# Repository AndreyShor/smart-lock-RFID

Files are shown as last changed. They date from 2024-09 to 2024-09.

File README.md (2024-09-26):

# RFID Lock System

## RFID Lock on ESP 8266 (Wemos D1 min)

Wifi version of the RFID system is working on Wemos D1 mini microcontroler.

Templates for 3D Printer is stored in "Case" foldier. This files can be used to 3d print case for the lock.

We was using Arduino framework in combination with C++ libraries to write code for microcontroller.

<strong>LED Commands: </strong>
<ul>  
 <li>1 long blink - door is open </li>
 <li>2 short blings - incorrect RFID card </li>
 <li>Lock is blinking non stop - lock is trying to connect to WIFI </li>
 <li>8 medium blinks and 2 short - lock is connected to Wifi bet can't access server </li>
</ul>

## Lock Side Code - C/C++ and Arduino

Microcontroller is used on lock side. Basic Function of microcontroller is to get UID of a user and send it to the server for validation and manipulate a relay of the lock.

<strong> Link to all libraries for Microcontroller: </strong>

    \\cseesrv04\tech\CSEEprojects\RFID Lock Library

<ol>

<li> <strong> RFID_TAG_UID_PRINT.ino </strong>- contains code to display UID of the tag. </li> 

<li> <strong>DB</strong> - contains files of DB design </li> 

<li> <strong>Authentication_system.ino</strong> - contains authentication systemm for ESP8266, it is validate user by UID stored in in MySQL datbase and opening door for 5 seconds. Data encrypted done by using AES-128 algorithm </li> 

<li> <strong>ESPwifi_http_connection.ino</strong> - contains code to send request to connect to Wi-Fi, send request to backend server, store data in local memory 
<ol> You must specify
<li><strong>ssid</strong> of Wi-fi </li>
<li><strong>password</strong> of Wi-fi </li>
<li><strong>server IP</strong> and path to send request</li>

 </ol>

</li> 

</ol>

## Backend - Server Side,JavaScript Node.js, Express, MySQL 

Backend is written on Node.js + Express framework. MySQl is used as a Databse. Server is written on REST architecture.

Server is proccesing all request from the lock and grant access to space. 

Versions:
<ol>
<li>Node.js - 19.6.1</li>
<li>Npm - 9.5.0</li>
<li>Express - 4.18.2</li>
<li>mysql2 -3.2.0 </li>
 </ol>

All code you can find in a foldier "Server-Backend"

<strong>Environment and package varibles</strong> is specified in <strong>package.json</strong> file

<strong>Connection to MySQL <strong/> is specified in "DB/connect_db.js"

<strong>Authentication keys for AES is specified in "controller/cryptography.js"

You can <strong>create database and table </strong>by running create_db.sql

All <strong>server routes </strong> is specified in routes.js

You can start server by typing "npm start" or "node server.js"

### How to install node.js and npm

#### Short Way

<p>You should be able to install all libraries by copying project from /Server-Backend
Use this 2 commands to install everething, Node and NPM should be installed for this method </p>

    1. npm init
    2. npm install or npm i 

#### Long Way

<ol>
<li> Node.js and NPM - follow this link and install LTS version of node.js </li>
    https://nodejs.org/en/download

<li>NVM (Node Version Manager ) - install NVM to change version of Node.js to 19.6.1 or any others. Code should work on any versions of Node </li>

    https://github.com/nvm-sh/nvm

    Command to install nvm:
    npm i -g nvm

<li>Express - install express, this framework simplify routing on Node.js </li>
    https://expressjs.com/
    npm i -g express

<li>MySQL library</li>
    npm i mysql2
    https://www.npmjs.com/package/mysql2
 </ol>

## Electrical part of RFID lock 

Box, lead and frame was design for this project. Tou can find .stl and .gz files in <strong> Case foldier </strong>

Schematic of circuit:

Diagram

### Parts
<ol>
<li><strong> RELAY</strong> - KY-019 5V 1-Channel Relay Board Module for Arduino IOT, cost about 2 pounds </li>
<li><strong> Microcontroller</strong> - ESP8266, cost about 8 pounds </li>
<li><strong> RFID Reader</strong> - AZDelivery RFID Kit - MFRC522, about 4.5 pounds  </li>
<li><strong> DC-DC converter</strong> - 20W Adjustable DC-DC Buck Converter with Digital Display about 4.5 pounds </li>
<li><strong> Fuse</strong> </li>
<li><strong> Wifi Box</strong> - 3D printed </li>
<li><strong> Wifi Box Lead</strong> - 3D printed </li>
<li><strong> Wifi Box Frame</strong> - 3D printed </li>
<li><strong> Diode for lock</strong> - 0.2 pound </li>
<li><strong> Total Cost of RFID soluion:</strong> +- 20 pounds </li>

<li><strong>Lock</strong> - GEM GK310LS 12 VDC Electric Release, aboyt 50-60 pounds </li>
<li><strong>Total Cost of RFID soluion + Lock for 1 door:</strong> +- 70 - 80 pounds </li>
</ol>

### Pins

<p>You can find pins connection for ESP8266 and RFID Reader in ESP8266 Pins.docx</p>

# Encryption - C Language

## Encryption is build by using BearSSL framework written on C
<p>Link: </p>
<p>https://bearssl.org/ </p>

<p>I was using AES-128-CBC method of encryption.</p>

<p>Youd should make some minor changes to run code with ESP8266 </p>
<ul>

<li>0. Install MFRC522 for scanner </li>

<li>1. Add Base64A.h and Base64A.cpp files to C:\Users\%UserName%\AppData\Local\Arduino15\packages\esp8266\hardware\esp8266\3.1.2\cores\esp8266</li>
<li>2. Change Secret Key and IV Vector in Authentication_system.ino</li>

    uint8_t cipher_key[16] = {0, 2, 4, 3, 4, 5, 6, 7, 8, 9, 10, 11, 12, 13, 14, 15};
    uint8_t cipher_iv[16] = {0, 6, 6, 3, 4, 5, 6, 7, 8, 9, 10, 11, 12, 13, 14, 15};

<li>3. Change Secret Key and IV Vector cryptography.js</li>

    var cipher_key = Buffer.from([0, 2, 4, 3, 4, 5, 6, 7, 8, 9, 10, 11, 12, 13, 14, 15]);
    var cipher_iv = Buffer.from([0, 6, 6, 3, 4, 5, 6, 7, 8, 9, 10, 11, 12, 13, 14, 15]);

<li>3. Change IP Adress and port of server in Authentication_system.ino</li>

    String serverName = "http://192.168.0.102:8080/validateAccess";

<li>4. Change Wifi SSID and PASS in Authentication_system.ino</li>

    char* ssid = "TP-LINK_6926";
    char* password = "29328123";

</ul>

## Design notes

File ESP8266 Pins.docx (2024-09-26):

# RC522 Pins

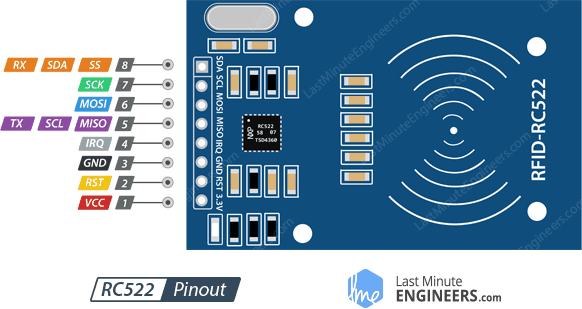
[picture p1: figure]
RC522 RFID Reader Writer Module Pinout

SS / SDA / Rx pin acts as a signal input when the SPI interface is enabled, as serial data when the I2C interface is enabled and as a serial data input when the UART interface is enabled. This pin is usually marked by encasing the pin in a square so that it can be used as a reference to identify other pins.

(IN) D2

SCK (Serial Clock) accepts the clock pulses provided by the SPI bus master i.e. Arduino. (Synchronization between controller and Arduino) D5

MISO / SCL / Tx pin acts as master-in-slave-out when SPI interface is enabled, as serial clock when I2C interface is enabled and as serial data output when the UART interface is enabled. (OUT) D6

IRQ is an interrupt pin that alerts the microcontroller when an RFID tag is in the vicinity. (Interrupt) NONE

GND is the ground pin and needs to be connected to the GND pin on the Arduino. (ground) GND

RST is an input for reset and power-down. When this pin goes low the module enters power-down mode. In which the oscillator is turned off and the input pins are disconnected from the outside world. Whereas the module is reset on the rising edge of the signal. (Shut down, reset) RST D1

VCC supplies power to the module. This can be anywhere from 2.5 to 3.3 volts. You can connect it to the 3.3V output from your Arduino. But remember that connecting it to the 5V pin will probably destroy your module! (power) 3.3V

ESP8266 Pin reference

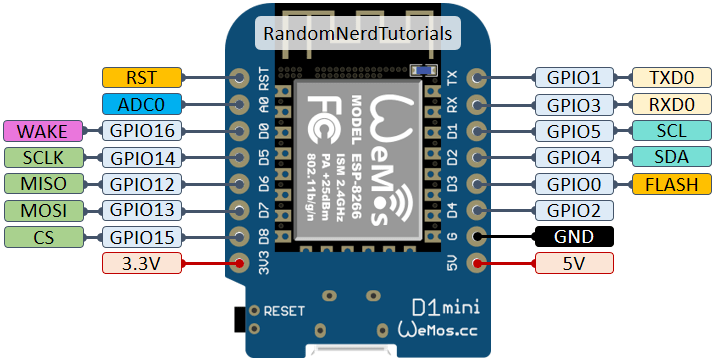
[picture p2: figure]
ESP8266 Pinout Reference: Which GPIO pins should you use? | Random Nerd Tutorials

Pin | Function | ESP-8266 Pin
TX | TXD | TXD
RX | RXD | RXD
A0 | Analog input, max 3.3V input | A0
D0 | IO | GPIO16
D1 | IO, SCL | GPIO5
D2 | IO, SDA | GPIO4
D3 | IO, 10k Pull-up | GPIO0
D4 | IO, 10k Pull-up, BUILTIN_LED | GPIO2
D5 | IO, SCK | GPIO14
D6 | IO, MISO | GPIO12
D7 | IO, MOSI | GPIO13
D8 | IO, 10k Pull-down, SS | GPIO15
G | Ground | GND
5V | 5V | -
3V3 | 3.3V | 3.3V
RST | Reset | RST

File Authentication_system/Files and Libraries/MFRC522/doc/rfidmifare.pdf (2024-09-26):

## Using a MFRC522 reader to read and write MIFARE RFID cards

on ARDUINO through the MFRC522 library BY COOQROBOT.
Mario Capurso (m.capurso@libero.it)

MIFARE is the NXP Semiconductors-owned trademark of a series of chips widely
used in contactless smart cards and proximity cards. According to the producers, billions of smart card chips and many millions of reader modules have been sold. [1]

The technology is owned by NXP Semiconductors (spin off from Philips Electronics in 2006) with headquarters in Eindhoven, Netherlands, and main business sites in Nijmegen, Netherlands, and Hamburg, Germany.

The MIFARE name covers proprietary technologies based upon various levels of the ISO/IEC 14443 Type A 13.56 MHz contactless smart card standard.
The MIFARE name (derived from the term MIkron FARE Collection System) covers
seven different kinds of contactless cards.

MIFARE Classic employs a proprietary protocol compliant to parts (but not all) of ISO/IEC 14443-3 Type A, with an NXP proprietary security protocol for authentication and ciphering.

The MIFARE Classic card is fundamentally just a memory storage device, where the memory is divided into segments and blocks with simple security mechanisms for access control. They are ASIC-based and have limited computational power. Thanks
to their reliability and low cost, those cards are widely used for electronic wallet, access control, corporate ID cards, transportation or stadium ticketing.

The MIFARE Classic 1K offers 1024 bytes of data storage, split into 16 sectors; each sector is protected by two different keys, called A and B. Each key can be programmed to allow operations such as reading, writing, increasing valueblocks, etc. MIFARE Classic 4K offers 4096 bytes split into forty sectors, of which 32 are same size as in the 1K with eight more that are quadruple size sectors. MIFARE Classic mini offers 320 bytes split into five sectors.

For each of these card types, 16 bytes per sector are reserved for the keys and access conditions and can not normally be used for user data. Also, the very first 16 bytes contain the serial number of the card and certain other manufacturer data and are read only. That brings the net storage capacity of these cards down to 752 bytes for MIFARE Classic 1k, 3440 bytes for MIFARE Classic 4k, and 224 bytes for Mini. It uses an NXP proprietary security protocol (Crypto-1) for authentication and ciphering.

The encryption used by the MIFARE Classic card uses a 48 bit key. [18]
A presentation by Henryk Plötz and Karsten Nohl[19] at the Chaos Communication Congress in December 2007 described a partial reverse-engineering of the algorithm used in the MIFARE Classic chip. Abstract and slides[20] are available online. A paper that describes the process of reverse engineering this chip was published at the August 2008 USENIX security conference.[21] (https://www.usenix.org/legacy/events/sec08/tech/full_papers/nohl/nohl.pdf)

In March 2008 the Digital Security[22] research group of the Radboud University Nijmegen made public that they performed a complete reverse-engineering and
were able to clone and manipulate the contents of an OV-Chipkaart which is a MIFARE Classic card.[23] (http://www.cs.ru.nl/~flaviog/publications/Talk.Mifare.pdf) For demonstration they used the Proxmark device, a 125 kHz / 13.56 MHz research instrument.[24] The schematics and software are released under the free GNU General Public License by Jonathan Westhues in 2007. They demonstrate it is even possible to perform card-only attacks using just an ordinary stock-commercial NFC reader in combination with the libnfc library.

In April 2009 new and better card-only attack on MIFARE Classic has been
found. It was first announced at the Rump session of Eurocrypt 2009.[35] This attack was presented at SECRYPT 2009.[36] The full description of this latest and fastest attack to date can also be found in the IACR preprint archive.[37] The new attack improves by a factor of more than 10 all previous card-only attacks on MIFARE Classic, has instant running time, and it does not require a costly precomputation.

The new attack allows to recover the secret key of any sector of MIFARE Classic card via wireless interaction, within about 300 queries to the card. It can then be combined with the nested authentication attack in the Nijmegen Oakland paper to recover subsequent keys almost instantly. Both attacks combined and with the right hardware equipment such as Proxmark3, one should be able to clone any MIFARE Classic card in not more than 10 seconds. This is much faster than previously thought.

The MFRC522 is a highly integrated reader/writer IC for contactless communication at 13.56 MHz. The MFRC522 reader supports ISO/IEC 14443 A/MIFARE mode.
The MFRC522’s internal transmitter is able to drive a reader/writer antenna designed to communicate with ISO/IEC 14443 A/MIFARE cards and transponders without additional active circuitry. The receiver module provides a robust and efficient implementation for demodulating and decoding signals from ISO/IEC 14443 A/MIFARE compatible cards and transponders. The digital module manages the complete ISO/IEC 14443 A framing and error detection (parity and CRC) functionality.

The MFRC522 supports all variants of the MIFARE Mini, MIFARE 1K, MIFARE 4K, MIFARE Ultralight, MIFARE DESFire EV1 and MIFARE Plus RF identification protocols. To aid readability throughout this data sheet, the MIFARE Mini,

MIFARE 1K, MIFARE 4K, MIFARE Ultralight, MIFARE DESFire EV1 and MIFARE Plus products and protocols have the generic name MIFARE.

The following host interfaces are provided:

- Serial Peripheral Interface (SPI)
- Serial UART (similar to RS232 with voltage levels dependant on pin voltage supply)
- I2C-bus interface

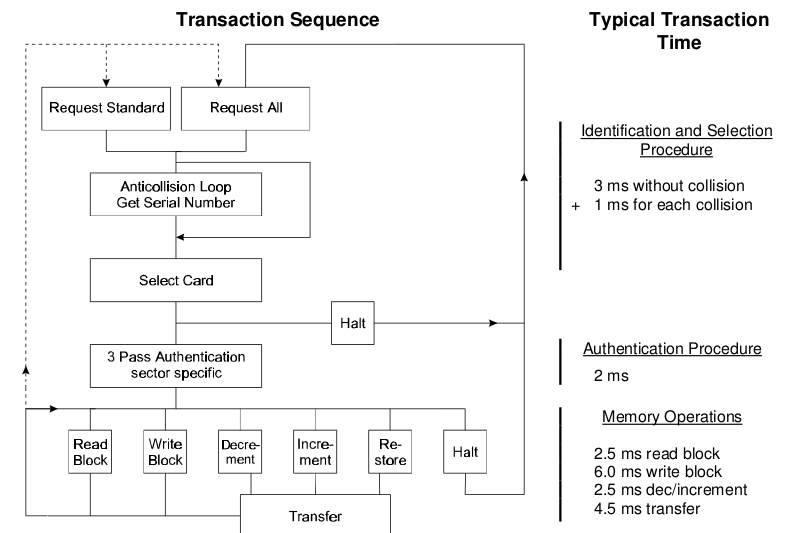
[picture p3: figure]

Answer to Request :

With the Answer to Request sequence the MIFARE® RWD (Read Write Device) requests all MIFARE® cards in the antenna field. When a card is in the operating range of a RWD, the RWD continues communication with the appropriate protocol.

Anticollision loop
In the Anticollision loop the serial number of the card is read. If there are several cards in the operating range of a RWD they can be distinguished by their different serial numbers and one can be selected (Select card) for further transactions. The unselected cards return to the standby mode and wait for a new Answer to Request and Anticollision loop.

Select Card
With the Select Card command the RWD selects one individual card for further authentication and memory related operations. The card returns the Answer to Select (ATS) code, which determines the individual type of the selected card.

Access Specification
After identification and selection of one card the RWD specifies the memory location of the following access.

Three Pass Authentication
The appropriate access key for the previously specified access is used for 3 Pass Authentication. Any communication after authentication is automatically encrypted at the sender and decrypted by the receiver.

Read/Write

After authentication any of the following operations may be performed:

READ | reads one block
WRITE | writes one block
DECREMENT | decrements the contents of one block and stores the result
| in the data-register
INCREMENT | increments the contents of one block and stores the result
| in the data-register
TRANSFER | writes the contents of the data-register to one block
RESTORE | stores the contents of one block in the data-register

The MF1ICS50 IC of a Mifare Classic has integrated a 8192 Bit EEPROM which is split into 16 sectors with 4 blocks. One block consists of 16 bytes (1 Byte = 8 Bit).

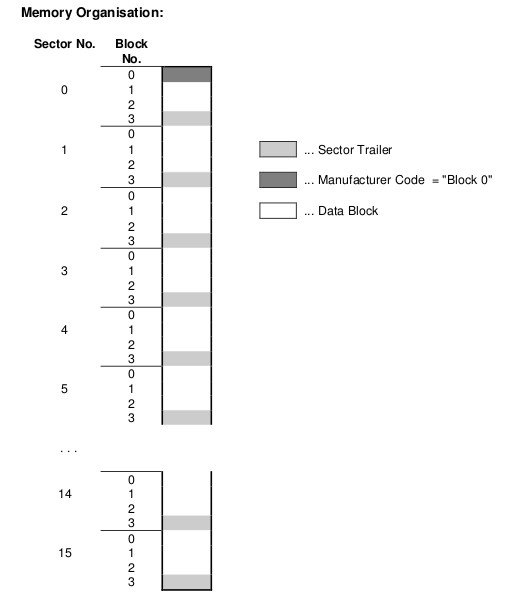
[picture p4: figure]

Manufacturer Code (Block 0 of Sector 0)

The first block of the memory is reserved for manufacturer data like 32 bit serial number. This is a read only block. In many documents it is named "Block 0".

Data Block (Block 0 to 3 except "Block 0")

Access conditions for the Data Blocks are defined in the Sector Trailers. According to these conditions data can be read, written, incremented, decremented, transferred or restored either with Key A, Key B or never.

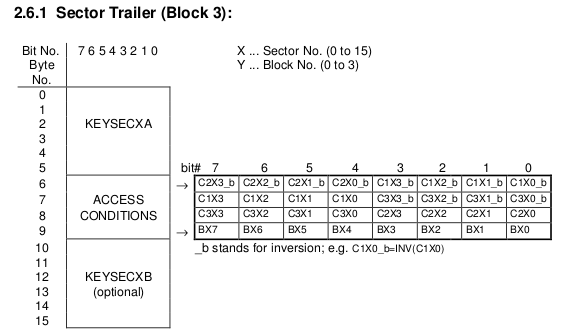
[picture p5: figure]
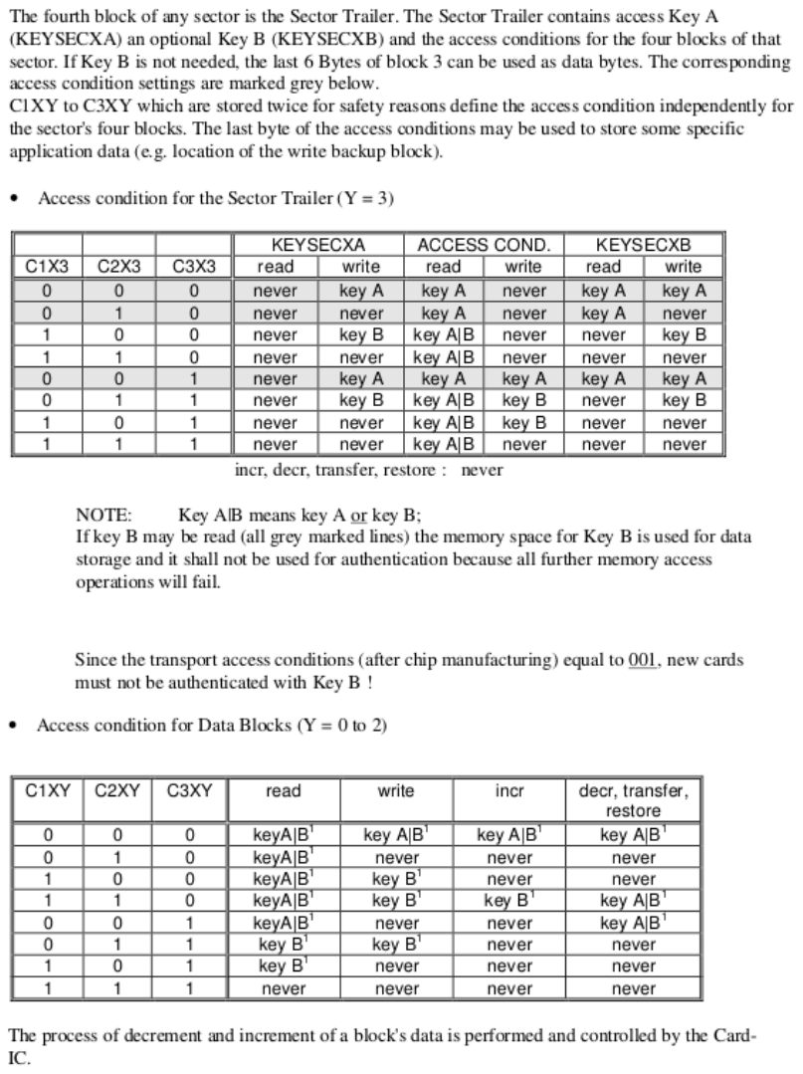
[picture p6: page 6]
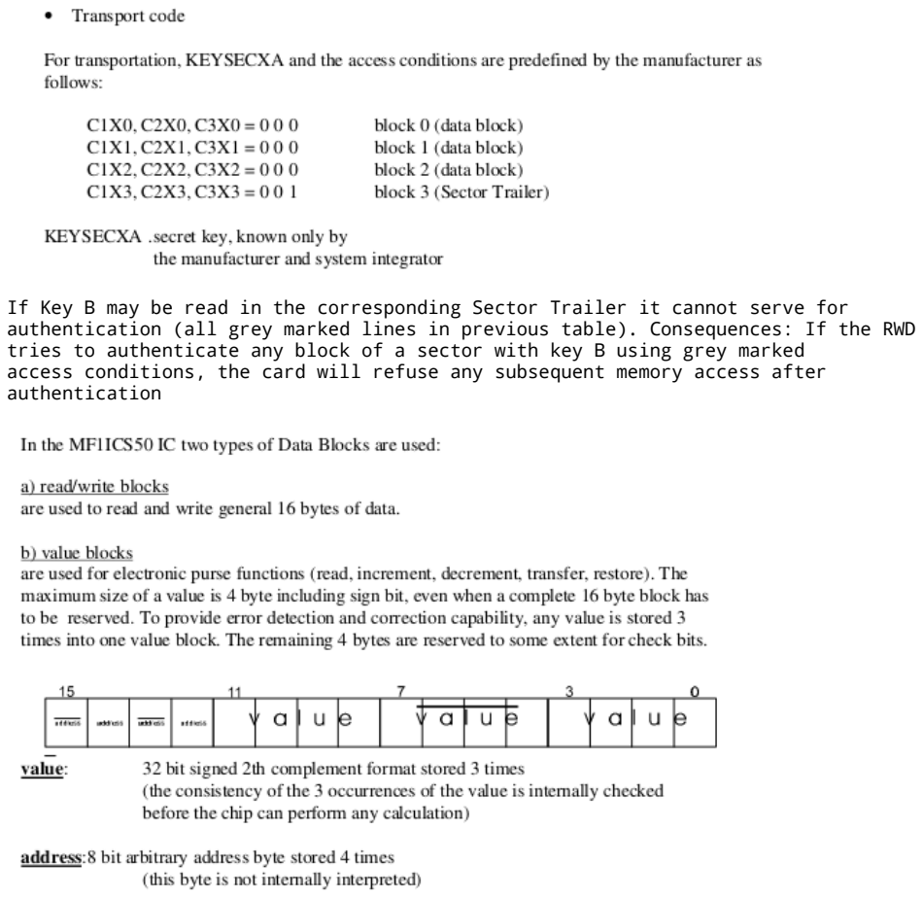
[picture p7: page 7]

If Key B may be read in the corresponding Sector Trailer it cannot serve for authentication (all grey marked lines in previous table). Consequences: If the RWD tries to authenticate any block of a sector with key B using grey marked
access conditions, the card will refuse any subsequent memory access after authentication

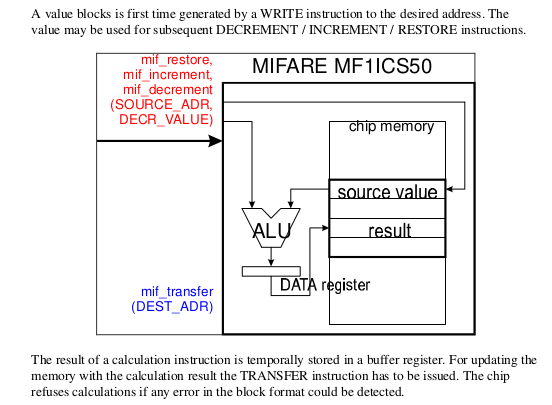
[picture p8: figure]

The described memory organization makes it possible to appoint different sectors to different applications and to prevent data corruption by using application specific secret keys. Keys can only be altered by a RWD which has stored the actual Key A or Key B if this is allowed according to access conditions. Otherwise the actual key cannot be changed anymore.

Before the execution of a command the correct format of the Access Conditions is checked by the Card-IC. Thus, when programming the Sector Trailer the card needs to be fixed within the operating range of a RWD's antenna to prevent interruption of the write operation because any unsuccessful write operation may lead to blocking the whole sector.

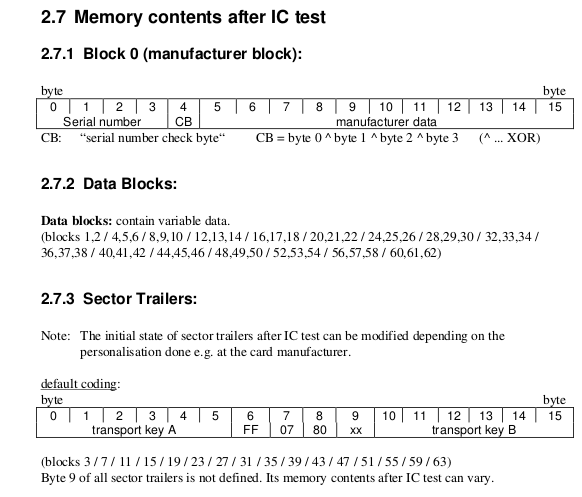
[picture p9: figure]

## MFRC522.h – A Library to use ARDUINO RFID MODULE KIT 13.56

MHZ BY COOQROBOT.

There are three hardware components involved:

1) The micro controller: An Arduino
2) The PCD (Proximity Coupling Device): NXP MFRC522 Contactless Reader IC
3) The PICC (short for Proximity Integrated Circuit Card): A card or tag using the ISO 14443A interface, eg Mifare or NTAG203.

MIFARE Classic 1K (MF1S503x):

Has 16 sectors * 4 blocks/sector * 16 bytes/block = 1024 bytes. The blocks are numbered 0-63.

Block 3 in each sector is the Sector Trailer.
* | Bytes 0-5: | Key A
* | Bytes 6-8: | Access Bits
* | Bytes 9: | User data
* | Bytes 10-15: Key B (or user data)

Block 0 is read only manufacturer data.

To access a block, an authentication using a key from the block's sector must be performed first.

Example: To read from block 10, first authenticate using a key from sector 3 (blocks 8-11).

All keys are set to FFFFFFFFFFFFh at chip delivery.

Warning: Please read section 8.7 "Memory Access". It includes this text: if the PICC detects a format violation the whole sector is irreversibly blocked.

To use a block in "value block" mode (for Increment/Decrement operations) you need to change the sector trailer. Use PICC_SetAccessBits() to calculate the bit patterns.

Commands sent to the PICC.

The commands used by the PCD to manage communication with several PICCs (ISO 14443-3, Type A, section 6.4)

PICC_CMD_REQA = 0x26,
REQuest command, Type A. Invites PICCs in state IDLE to go to READY and prepare for anticollision or selection. 7 bit frame.
PICC_CMD_WUPA = 0x52,
Wake-UP command, Type A. Invites PICCs in state IDLE and HALT to go to READY(*) and prepare for anticollision or selection. 7 bit frame.
PICC_CMD_CT = 0x88,
Cascade Tag. Not really a command, but used during anti collision. PICC_CMD_SEL_CL1 = 0x93,
Anti collision/Select, Cascade Level 1
PICC_CMD_SEL_CL2 = 0x95,
Anti collision/Select, Cascade Level 2 PICC_CMD_SEL_CL3 = 0x97,
Anti collision/Select, Cascade Level 3
PICC_CMD_HLTA = 0x50,
HaLT command, Type A. Instructs an ACTIVE PICC to go to state HALT.

The commands used for MIFARE Classic
Use PCD_MFAuthent to authenticate access to a sector, then use these commands to read/write/modify the blocks on the sector.
The read/write commands can also be used for MIFARE Ultralight.

PICC_CMD_MF_AUTH_KEY_A = 0x60,
Perform authentication with Key A
PICC_CMD_MF_AUTH_KEY_B = 0x61,
Perform authentication with Key B
PICC_CMD_MF_READ | = 0x30,
Reads one 16 byte block from the authenticated sector of the PICC. Also used for MIFARE Ultralight.
PICC_CMD_MF_WRITE | = 0xA0,
Writes one 16 byte block to the authenticated sector of the PICC. Called "COMPATIBILITY WRITE" for MIFARE Ultralight.
PICC_CMD_MF_DECREMENT = 0xC0,
Decrements the contents of a block and stores the result in the internal data register.
PICC_CMD_MF_INCREMENT = 0xC1,
Increments the contents of a block and stores the result in the internal data register.
PICC_CMD_MF_RESTORE | = 0xC2,
Reads the contents of a block into the internal data register. PICC_CMD_MF_TRANSFER = 0xB0,
Writes the contents of the internal data register to a block.

List of the functions in the library

Functions for setting up the Arduino

MFRC522(byte chipSelectPin, byte resetPowerDownPin);
void setSPIConfig();

Basic interface functions for communicating with the MFRC522

void PCD_WriteRegister(byte reg, byte value);
void PCD_WriteRegister(byte reg, byte count, byte *values);
byte PCD_ReadRegister(byte reg);
void PCD_ReadRegister(byte reg, byte count, byte *values, byte rxAlign = 0); void setBitMask(unsigned char reg, unsigned char mask);
void PCD_SetRegisterBitMask(byte reg, byte mask);
void PCD_ClearRegisterBitMask(byte reg, byte mask);
byte PCD_CalculateCRC(byte *data, byte length, byte *result);

Functions for manipulating the MFRC522

void PCD_Init();
void PCD_Reset();
void PCD_AntennaOn();

Functions for communicating with PICCs

byte PCD_TransceiveData(byte *sendData, byte sendLen, byte *backData, byte *backLen, byte *validBits = NULL, byte rxAlign = 0, bool checkCRC = false);

byte PCD_CommunicateWithPICC(byte command, byte waitIRq, byte *sendData, byte sendLen, byte *backData = NULL, byte *backLen = NULL, byte *validBits = NULL, byte rxAlign = 0, bool checkCRC = false);

byte PICC_RequestA(byte *bufferATQA, byte *bufferSize);
byte PICC_WakeupA(byte *bufferATQA, byte *bufferSize);
byte PICC_REQA_or_WUPA( byte command, byte *bufferATQA, byte *bufferSize); byte PICC_Select(Uid *uid, byte validBits = 0);
byte PICC_HaltA();

Functions for communicating with MIFARE PICCs

byte PCD_Authenticate(byte command, byte blockAddr, MIFARE_Key *key, Uid *uid); void PCD_StopCrypto1();
byte MIFARE_Read(byte blockAddr, byte *buffer, byte *bufferSize);
byte MIFARE_Write(byte blockAddr, byte *buffer, byte bufferSize);
byte MIFARE_Decrement(byte blockAddr, long delta);
byte MIFARE_Increment(byte blockAddr, long delta);
byte MIFARE_Restore(byte blockAddr);
byte MIFARE_Transfer(byte blockAddr);
byte MIFARE_Ultralight_Write(byte page, byte *buffer, byte bufferSize);

Support functions

byte PCD_MIFARE_Transceive( byte *sendData, byte sendLen, bool acceptTimeout = false);
const char *GetStatusCodeName(byte code);
byte PICC_GetType(byte sak);
const char *PICC_GetTypeName(byte type);
void PICC_DumpToSerial(Uid *uid);
void PICC_DumpMifareClassicToSerial(Uid *uid, byte piccType, MIFARE_Key *key);
void PICC_DumpMifareClassicSectorToSerial(Uid *uid, MIFARE_Key *key, byte sector); void PICC_DumpMifareUltralightToSerial();
void MIFARE_SetAccessBits(byte *accessBitBuffer, byte g0, byte g1, byte g2, byte g3);

Convenience functions - does not add extra functionality

bool PICC_IsNewCardPresent();
bool PICC_ReadCardSerial();

Detailed documentation – enum and structures

PICC types we can detect. Remember to update PICC_GetTypeName() if you add more.

enum PICC_Type

Return codes from the functions in this class. Remember to update GetStatusCodeName() if you add more.

enum StatusCode

A struct used for passing the UID of a PICC.

typedef struct {
byte | size; | Number of bytes in the UID. 4, 7 or 10.
byte | uidByte[10];
byte | sak; | The SAK (Select acknowledge) byte returned
| | from the PICC after successful selection.
} Uid

A struct used for passing a MIFARE Crypto1 key

typedef struct {
byte | keyByte[MF_KEY_SIZE];
} MIFARE_Key;

Example:
// Prepare key - all keys are set to FFFFFFFFFFFFh at chip delivery from the factory. MFRC522::MIFARE_Key key;
for (byte i = 0; i < 6; i++) key.keyByte[i] = 0xFF;

Member variables

Uid uid; | Used by PICC_ReadCardSerial().

Detailed documentation – functions

+Create object instance
MFRC522(
byte chipSelectPin, Arduino pin used for SPI chip select byte resetPowerDownPin Arduino pin used for SPI reset
);
Example:
#include <SPI.h>

#include <MFRC522.h>

#define SS_PIN 10 //Arduino Uno

#define RST_PIN 9

MFRC522 mfrc522(SS_PIN, RST_PIN); | // Create MFRC522 instance.

+Initializes the MFRC522 chip.
void MFRC522::PCD_Init()
Example:
void setup() {
Serial.begin(9600); | // Init serial communications with PC
SPI.begin(); | // Init SPI bus
mfrc522.PCD_Init(); | // Init MFRC522 card
}

+Set SPI bus to work with MFRC522 chip.

Please call this function if you have changed the SPI config since the MFRC522 constructor was run.

void MFRC522::setSPIConfig()

+Performs a soft reset on the MFRC522 chip and waits for it to be ready again. void MFRC522::PCD_Reset()

+Turns the antenna on by enabling pins TX1 and TX2.
After a reset these pins are disabled.
void MFRC522::PCD_AntennaOn()

+Transmits a REQuest command, Type A. Invites PICCs in state IDLE to go to READY and prepare for anticollision or selection. 7 bit frame.
Beware: When two PICCs are in the field at the same time I often get STATUS_TIMEOUT -probably due do bad antenna design.
return STATUS_OK on success, STATUS_??? otherwise.
byte MFRC522::PICC_RequestA(
byte *bufferATQA, The buffer to store the ATQA (Answer to request) in
byte *bufferSize Buffer size, at least two bytes. Also number of bytes returned if STATUS_OK.

+Transmits a Wake-UP command, Type A. Invites PICCs in state IDLE and HALT to go to READY(*) and prepare for anticollision or selection. 7 bit frame.
Beware: When two PICCs are in the field at the same time I often get STATUS_TIMEOUT -probably due do bad antenna design.
return STATUS_OK on success, STATUS_??? otherwise.
byte MFRC522::PICC_WakeupA(
byte *bufferATQA, The buffer to store the ATQA (Answer to request) in
byte *bufferSize Buffer size, at least two bytes. Also number of bytes returned if STATUS_OK.

+Transmits SELECT/ANTICOLLISION commands to select a single PICC.
Before calling this function the PICCs must be placed in the READY(*) state by calling PICC_RequestA() or PICC_WakeupA().
On success:

-The chosen PICC is in state ACTIVE(*) and all other PICCs have returned to state IDLE/HALT. (Figure 7 of the ISO/IEC 14443-3 draft.)
-The UID size and value of the chosen PICC is returned in *uid along with the SAK.

A PICC UID consists of 4, 7 or 10 bytes.
Only 4 bytes can be specified in a SELECT command, so for the longer UIDs two or three iterations are used:
UID size | Number of UID bytes | Cascade levels | Example of PICC
======== | =================== | ============== | ===============
single | 4 | 1 | MIFARE Classic
double | 7 | 2 | MIFARE Ultralight
triple | 10 | 3 | Not currently in use?

return STATUS_OK on success, STATUS_??? otherwise.
byte MFRC522::PICC_Select(
Uid *uid, | Pointer to Uid struct. Normally output, but can also
be used to supply a known UID.
byte validBits | The number of known UID bits supplied in *uid.

Normally 0. If set you must also supply uid->size.

Description of buffer structure:

Byte 0: SEL | Indicates the Cascade Level: PICC_CMD_SEL_CL1,
PICC_CMD_SEL_CL2 or PICC_CMD_SEL_CL3
Byte 1: NVB | Number of Valid Bits (in complete command, not just the UID):
High nibble: complete bytes, Low nibble: Extra bits.
Byte 2: UID-data or CT See explanation below. CT means Cascade Tag.
Byte 3: UID-data
Byte 4: UID-data
Byte 5: UID-data
Byte 6: BCC | Block Check Character - XOR of bytes 2-5
Byte 7: CRC_A
Byte 8: CRC_A

The BCC and CRC_A is only transmitted if we know all the UID bits of the current Cascade Level.
Description of bytes 2-5: (Section 6.5.4 of the ISO/IEC 14443-3 draft: UID contents and cascade levels)
UID size | Cascade level | Byte2 Byte3 Byte4 Byte5
======== | ============= | ===== ===== ===== =====
4 bytes | 1 | uid0 uid1 uid2 uid3

7 bytes | 1 | CT | uid0 uid1 uid2
2 | uid3 uid4 uid5 uid6
10 bytes | 1 | CT | uid0 uid1 uid2
| 2 | CT | uid3 uid4 uid5

+Instructs a PICC in state ACTIVE(*) to go to state HALT. return STATUS_OK on success, STATUS_??? otherwise.
byte PICC_HaltA();
Example:
// Halt PICC
mfrc522.PICC_HaltA();

+Executes the MFRC522 MFAuthent command.
This command manages MIFARE authentication to enable a secure communication to any MIFARE Mini, MIFARE 1K and MIFARE 4K card.
The authentication is described in the MFRC522 datasheet section 10.3.1.9 and http://www.nxp.com/documents/data_sheet/MF1S503x.pdf section 10.1. for use with MIFARE Classic PICCs.
The PICC must be selected - ie in state ACTIVE(*) - before calling this function. Remember to call PCD_StopCrypto1() at the end of communication with the authenticated PICC - otherwise no new communications can start.
All keys are set to FFFFFFFFFFFFh at chip delivery.
return STATUS_OK on success, STATUS_??? otherwise. Probably STATUS_TIMEOUT if you supply the wrong key.
byte MFRC522::PCD_AuthenticateI(
byte command, | PICC_CMD_MF_AUTH_KEY_A or PICC_CMD_MF_AUTH_KEY_B
byte blockAddr, | The block number. See numbering in the comments in
| the .h file.
MIFARE_Key *key, | Pointer to the Crypto1 key to use (6 bytes)
Uid *uid | Pointer to Uid struct. The first 4 bytes of the UID
| is used.
)
Example:
MFRC522::MIFARE_Key key;
for (byte i = 0; i < 6; i++) key.keyByte[i] = 0xFF; byte trailerBlock = 7;
byte status;
if ( ! mfrc522.PICC_ReadCardSerial()) return;
status = mfrc522.PCD_Authenticate(MFRC522::PICC_CMD_MF_AUTH_KEY_A, trailerBlock, &key, &(mfrc522.uid));
if (status != MFRC522::STATUS_OK) {
Serial.print("PCD_Authenticate() failed: "); Serial.println(mfrc522.GetStatusCodeName(status)); return;
}

+Used to exit the PCD from its authenticated state.
Remember to call PCD_StopCrypto1() at the end of communication with the authenticated PICC - otherwise no new communications can start.
void MFRC522::PCD_StopCrypto1()
Example:
// Stop encryption on PCD
mfrc522.PCD_StopCrypto1();

+Reads 16 bytes (+ 2 bytes CRC_A) from the active PICC.
For MIFARE Classic the sector containing the block must be authenticated before calling this function.
For MIFARE Ultralight only addresses 00h to 0Fh are decoded.
* The MF0ICU1 returns a NAK for higher addresses.

* The MF0ICU1 responds to the READ command by sending 16 bytes starting from
the page address defined by the command argument.
* For example; if blockAddr is 03h then pages 03h, 04h, 05h, 06h are returned.
* A roll-back is implemented: If blockAddr is 0Eh, then the contents of pages 0Eh, 0Fh, 00h and 01h are returned.
The buffer must be at least 18 bytes because a CRC_A is also returned.
Checks the CRC_A before returning STATUS_OK.
return STATUS_OK on success, STATUS_??? otherwise.
byte MFRC522::MIFARE_Read(
byte blockAddr, | MIFARE Classic: The block (0-0xff) number.
| MIFARE Ultralight: The first page to return data from.
byte *buffer, | The buffer to store the data in

byte *bufferSize Buffer size, at least 18 bytes. Also number of bytes returned
| if STATUS_OK.
Example:
byte valueBlockA = 4; byte buffer[18]; byte size = sizeof(buffer);
byte status = mfrc522.MIFARE_Read(valueBlockA, buffer, &size);

+Writes 16 bytes to the active PICC.
For MIFARE Classic the sector containing the block must be authenticated before calling this function.
For MIFARE Ultralight the operation is called "COMPATIBILITY WRITE".
Even though 16 bytes are transferred to the Ultralight PICC, only the least significant 4 bytes (bytes 0 to 3) are written to the specified address. It is recommended to set the remaining bytes 04h to 0Fh to all logic 0.
return STATUS_OK on success, STATUS_??? otherwise.
byte MFRC522::MIFARE_Write(
byte blockAddr,
| MIFARE Classic: The block (0-0xff) number.
| MIFARE Ultralight: The page (2-15) to write to.
byte *buffer, | The 16 bytes to write to the PICC
byte bufferSize | Buffer size, must be at least 16 bytes. Exactly 16 bytes are
| written.
Example:
byte valueBlockA = 4;
byte value1Block[] = { 1,2,3,4, 5,6,7,8, 9,10,255,12, 13,14,15,16}; status = mfrc522.MIFARE_Write(valueBlockA, value1Block, 16);
if (status != MFRC522::STATUS_OK) {
Serial.print("MIFARE_Write() failed: "); Serial.println(mfrc522.GetStatusCodeName(status));
}

+MIFARE Decrement subtracts the delta from the value of the addressed block, and stores the result in a volatile memory.
For MIFARE Classic only. The sector containing the block must be authenticated before calling this function.
Only for blocks in "value block" mode, ie with access bits [C1 C2 C3] = [110] or [001].
Use MIFARE_Transfer() to store the result in a block.
return STATUS_OK on success, STATUS_??? otherwise.
byte MFRC522::MIFARE_Decrement(
byte blockAddr, | The block (0-0xff) number.
long delta | This number is subtracted from the value of block blockAddr.

+MIFARE Increment adds the delta to the value of the addressed block, and stores the result in a volatile memory.
For MIFARE Classic only. The sector containing the block must be authenticated before calling this function.
Only for blocks in "value block" mode, ie with access bits [C1 C2 C3] = [110] or

[001].
Use MIFARE_Transfer() to store the result in a block. return STATUS_OK on success, STATUS_??? otherwise.
byte MFRC522::MIFARE_Increment(
byte blockAddr, | The block (0-0xff) number.
long delta | This number is added to the value of block blockAddr.
Example:
// Add 1 to the value of valueBlockA and store the result in valueBlockA. byte valueBlockA = 5;
Serial.print("Adding 1 to value of block "); Serial.println(valueBlockA); byte status = mfrc522.MIFARE_Increment(valueBlockA, 1);
if (status != MFRC522::STATUS_OK) {
Serial.print("MIFARE_Increment() failed: "); Serial.println(mfrc522.GetStatusCodeName(status)); return;
}
status = mfrc522.MIFARE_Transfer(valueBlockA);
if (status != MFRC522::STATUS_OK) { Serial.print("MIFARE_Transfer() failed: "); Serial.println(mfrc522.GetStatusCodeName(status)); return;
}

+MIFARE Restore copies the value of the addressed block into a volatile memory.
For MIFARE Classic only. The sector containing the block must be authenticated before calling this function.
Only for blocks in "value block" mode, ie with access bits [C1 C2 C3] = [110] or [001].
Use MIFARE_Transfer() to store the result in a block.
return STATUS_OK on success, STATUS_??? otherwise.
byte MFRC522::MIFARE_Restore(
byte blockAddr The block (0-0xff) number.
The datasheet describes Restore as a two step operation, but does not explain what data to transfer in step 2.Doing only a single step does not work, so I chose to transfer 0L in step two.

+Helper function for the two-step MIFARE Classic protocol operations Decrement, Increment and Restore.
return STATUS_OK on success, STATUS_??? otherwise.
byte MFRC522::MIFARE_TwoStepHelper(
byte command, | The command to use
byte blockAddr, | The block (0-0xff) number.
long data | The data to transfer in step 2
)

+MIFARE Transfer writes the value stored in the volatile memory into one MIFARE Classic block.
For MIFARE Classic only. The sector containing the block must be authenticated before calling this function.
Only for blocks in "value block" mode, ie with access bits [C1 C2 C3] = [110] or [001].
return STATUS_OK on success, STATUS_??? otherwise.
byte MFRC522::MIFARE_Transfer(
byte blockAddr The block (0-0xff) number.

+Returns a string pointer to a status code name. const char *MFRC522::GetStatusCodeName(
byte code | One of the StatusCode enums.
code values | return values

STATUS_OK: | "Success."
STATUS_ERROR: | "Error in communication."
STATUS_COLLISION: | "Collision detected."
STATUS_TIMEOUT: | "Timeout in communication."
STATUS_NO_ROOM: | "A buffer is not big enough."
STATUS_INTERNAL_ERROR: "Internal error in the code. Should not happen."
STATUS_INVALID: | "Invalid argument."
STATUS_CRC_WRONG: | "The CRC_A does not match."
STATUS_MIFARE_NACK: | "A MIFARE PICC responded with NAK."
default: | "Unknown error"

Example:
Serial.println(mfrc522.GetStatusCodeName(status));

+Translates the SAK (Select Acknowledge) to a PICC type. return PICC_Type
byte MFRC522::PICC_GetType(
byte sak | The SAK byte returned from PICC_Select().
sak | return value
sak & 0x04 | PICC_TYPE_NOT_COMPLETE
0x09 | PICC_TYPE_MIFARE_MINI
0x08 | PICC_TYPE_MIFARE_1K
0x18 | PICC_TYPE_MIFARE_4K
0x00 | PICC_TYPE_MIFARE_UL
0x10 or 0x11 | PICC_TYPE_MIFARE_PLUS
0x01 | PICC_TYPE_TNP3XXX
sak & 0x20 | PICC_TYPE_ISO_14443_4
sak & 0x40 | PICC_TYPE_ISO_18092
else | PICC_TYPE_UNKNOWN

+Returns a string pointer to the PICC type name. const char *MFRC522::PICC_GetTypeName(
byte piccType | One of the PICC_Type enums.
piccType | return value
PICC_TYPE_ISO_14443_4 | "PICC compliant with ISO/IEC 14443-4"
PICC_TYPE_ISO_18092: | "PICC compliant with ISO/IEC 18092 (NFC)"
PICC_TYPE_MIFARE_MINI | "MIFARE Mini, 320 bytes"
PICC_TYPE_MIFARE_1K | "MIFARE 1KB"
PICC_TYPE_MIFARE_4K | "MIFARE 4KB"
PICC_TYPE_MIFARE_UL | "MIFARE Ultralight or Ultralight C"
PICC_TYPE_MIFARE_PLUS | "MIFARE Plus"
PICC_TYPE_TNP3XXX | "MIFARE TNP3XXX"
PICC_TYPE_NOT_COMPLETE "SAK indicates UID is not complete."
PICC_TYPE_UNKNOWN | "Unknown type”
Example:
Serial.println(mfrc522.PICC_GetTypeName(piccType));

+Dumps debug info about the selected PICC to Serial.
On success the PICC is halted after dumping the data.
For MIFARE Classic the factory default key of 0xFFFFFFFFFFFF is tried. void MFRC522::PICC_DumpToSerial(
Uid *uid Pointer to Uid struct returned from a successful PICC_Select(). Example:
mfrc522.PICC_DumpToSerial(&(mfrc522.uid));

+Dumps memory contents of a sector of a MIFARE Classic PICC.
Uses PCD_Authenticate(), MIFARE_Read() and PCD_StopCrypto1.

Always uses PICC_CMD_MF_AUTH_KEY_A because only Key A can always read the sector trailer access bits.
void MFRC522::PICC_DumpMifareClassicSectorToSerial(
Uid *uid, | Pointer to Uid struct returned from a successful PICC_Select()
MIFARE_Key *key, Key A for the sector.
byte sector | The sector to dump, 0..39.

+Calculates the bit pattern needed for the specified access bits. In the [C1 C2 C3] tuples C1 is MSB (=4) and C3 is LSB (=1).
void MFRC522::MIFARE_SetAccessBits(
byte *accessBitBuffer, Pointer to byte 6, 7 and 8 in the sector trailer.
| Bytes [0..2] will be set.
byte g0, | Access bits [C1 C2 C3] for block 0 (for sectors 0-31) or blocks 0-4 (for sectors 32-39)
byte g1, | Access bits C1 C2 C3] for block 1 (for sectors 0-31) or blocks 5-9 (for sectors 32-39)
byte g2, | Access bits C1 C2 C3] for block 2 (for sectors 0-31) or blocks 10-14 (for sectors 32-39)
byte g3 | Access bits C1 C2 C3] for the sector trailer, block 3 (for sectors 0-31) or block 15 (for sectors 32-39)

The access bits are stored in a peculiar fashion.
There are four groups:

g[3] Access bits for the sector trailer, block 3 (for sectors 0-31) or block 15 (for sectors 32-39)

g[2] Access bits for block 2 (for sectors 0-31) or blocks 10-14 (for sectors 32-39) g[1] Access bits for block 1 (for sectors 0-31) or blocks 5-9 (for sectors 32-39) g[0] Access bits for block 0 (for sectors 0-31) or blocks 0-4 (for sectors 32-39)

Each group has access bits [C1 C2 C3]. In this code C1 is MSB and C3 is LSB.
The four CX bits are stored together in a nibble cx and an inverted nibble cx_. Example:
// Sector trailer that defines blocks 5 and 6 as Value Blocks and enables key B. byte trailerBuffer[] = {255,255,255,255,255,255,0,0,0,0, 255,255,255,255,255,255}; // Keep default keys.
// g1=6(i.e.110) => block 5 value block. Key B write&increment, A or B decrement. // g2=6 => Same thing for block 6.
// g3=3 => Key B must be used to modify the Sector Trailer. Key B becomes valid. mfrc522.MIFARE_SetAccessBits(&trailerBuffer[6], 0, 6, 6, 3);

+Check if a card is present
bool MFRC522::PICC_IsNewCardPresent()
Returns true if a PICC responds to PICC_CMD_REQA.
Only "new" cards in state IDLE are invited. Sleeping cards in state HALT are ignored. Example:
// Look for new cards
if ( ! mfrc522.PICC_IsNewCardPresent()) return;

+Read Card Serial
bool MFRC522::PICC_ReadCardSerial()
Simple wrapper around PICC_Select.
Returns true if a UID could be read.The read UID is available in the class variable uid.
Remember to call PICC_IsNewCardPresent(), PICC_RequestA() or PICC_WakeupA() first. return true if one selected

Now a card is selected. The UID and SAK is in mfrc522.uid. Example:
Serial.print("Card UID:");
for (byte i = 0; i < mfrc522.uid.size; i++) { Serial.print(mfrc522.uid.uidByte[i] < 0x10 ? " 0" : " "); Serial.print(mfrc522.uid.uidByte[i], HEX);
}
// Dump PICC type
byte piccType = mfrc522.PICC_GetType(mfrc522.uid.sak); Serial.print("PICC type: "); Serial.println(mfrc522.PICC_GetTypeName(piccType));
if ( piccType != MFRC522::PICC_TYPE_MIFARE_MINI
&& piccType != MFRC522::PICC_TYPE_MIFARE_1K
&& | piccType != MFRC522::PICC_TYPE_MIFARE_4K) {
Serial.println("This sample only works with MIFARE Classic cards."); return;
}

How to convert a normal block into a value block
Usually a normal block has 000 access bits, while a value block has 110 access bits Example:
byte valueBlockA = 5;
byte valueBlockB = 6;
byte trailerBlock = 7;
// We need a sector trailer with blocks 5 and 6 as Value Blocks and enables key B. byte trailerBuffer[] = { 255,255,255,255,255,255,
| 0,0,0,0,255,255,255,255,255,255}; // Keep default keys.
// g1=6 => block 5 as value block. Key B to write&increment, A or B for decrement. // g2=6 => Same thing for block 6.
// g3=3 => Key B must be used to modify the Sector Trailer. Key B becomes valid. mfrc522.MIFARE_SetAccessBits(&trailerBuffer[6], 0, 6, 6, 3);
byte status = mfrc522.MIFARE_Write(trailerBlock, trailerBuffer, 16);
if (status != MFRC522::STATUS_OK) {
Serial.print("MIFARE_Write() failed: "); Serial.println(mfrc522.GetStatusCodeName(status));
return;
}

How to setup a Value Block with a value set to zero Example:
byte blockAddr=5;
byte valueBlock[] = {0,0,0,0, 255,255,255,255, 0,0,0,0,
| blockAddr,~blockAddr,blockAddr,~blockAddr };
byte status = mfrc522.MIFARE_Write(blockAddr, valueBlock, 16); if (status != MFRC522::STATUS_OK) { Serial.print("MIFARE_Write() failed: "); Serial.println(mfrc522.GetStatusCodeName(status));
}

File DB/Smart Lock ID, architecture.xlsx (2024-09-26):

 |  |  | User Table |  |  |  |  | Department Table
 |  |  | User ID (primar key) | Name | Surname | Department ID (public key) |  | Department ID (Primary key) | Department Name | Department Description
 |  |  | 1902817 | Andrejs | Sorstkins | CSEE |  | CSEE | School oF Computer Science | A lot of text
 |  |  | 1876314 | Ian | Dukes | CSEE |  | Py | Pshycology | A lot of text
 |  |  | 1368348 | Jon | Whitby | CSEE |  | My | Mathematics | A lot of text
 |  |  | 1358648 | Anton | Black | Py |  | …. | …. | ….
 |  |  | …. | …. | …. | …. |  | …. | …. | ….
 |  |  | …. | …. | …. | …. |  | …. | …. | ….
 |  |  | …. | …. | …. | …. |  | …. | …. | ….
 |  |  | …. | …. | …. | …. |  | …. | …. | ….
 |  |  | …. | …. | …. | …. |  | …. | …. | ….
User To Key Table |  |  |  | Location Table
User ID (Public key) | UID (primary key) |  |  | Location ID (primary key) | Location | Description | Room Number
1902817 | 5A C1 3F 16 |  |  | 1 | iSpace | Space for researh | 1N1.2.2
1876314 | 39 3F AF 87 |  |  | 2 | Laser arena | Space for lasers | 1N1.2.3
1368348 | 39 4F AF 55 |  |  | 3 | Robot Arena | Student Space for runnig robots | 1N1.2.4
1368348 | 39 3F AF 87 |  |  | 4 | Ian Office | You can find sometimes Ian there if you lucky | 1N1.2.5
1368348 | 5A C1 3F 16 |  |  | 5 | Andrejs & Joshua Offcie | Office of Robot arena technicains | 1N1.2.6
…. | …. |  |  | …. | …. | …. | ….
…. | …. |  |  | …. | …. | …. | ….
…. | …. |  |  | …. | …. | …. | ….
…. | …. |  |  | …. | …. | …. | ….
Lock to Key Table |  |  |  | Lock to Location Tbale (Main)
Lock ID (Public key) | UID (public key) | Access |  | Lock ID (primary key) | Location ID (public key)
11 | 5A C1 3F 16 | 1 |  | 11 | 1
22 | 39 3F AF 87 | 0 |  | 22 | 2
33 | 39 4F AF 55 | 1 |  | 33 | 3
44 | 39 3F AF 87 | 0 |  | 44 | 4
55 | 5A C1 3F 16 | 1 |  | 55 | 5
…. | …. | 1 |  | …. | ….
…. | …. | 1 |  | …. | ….
…. | …. | 0 |  | …. | ….
…. | …. | 1 |  | …. | ….
Query to take UID for a lock | Select LockIDToKey.UID From LockIDToKey Where LockID ="Given" AND LockIDToKey.Access == "1"
RED line is MVP

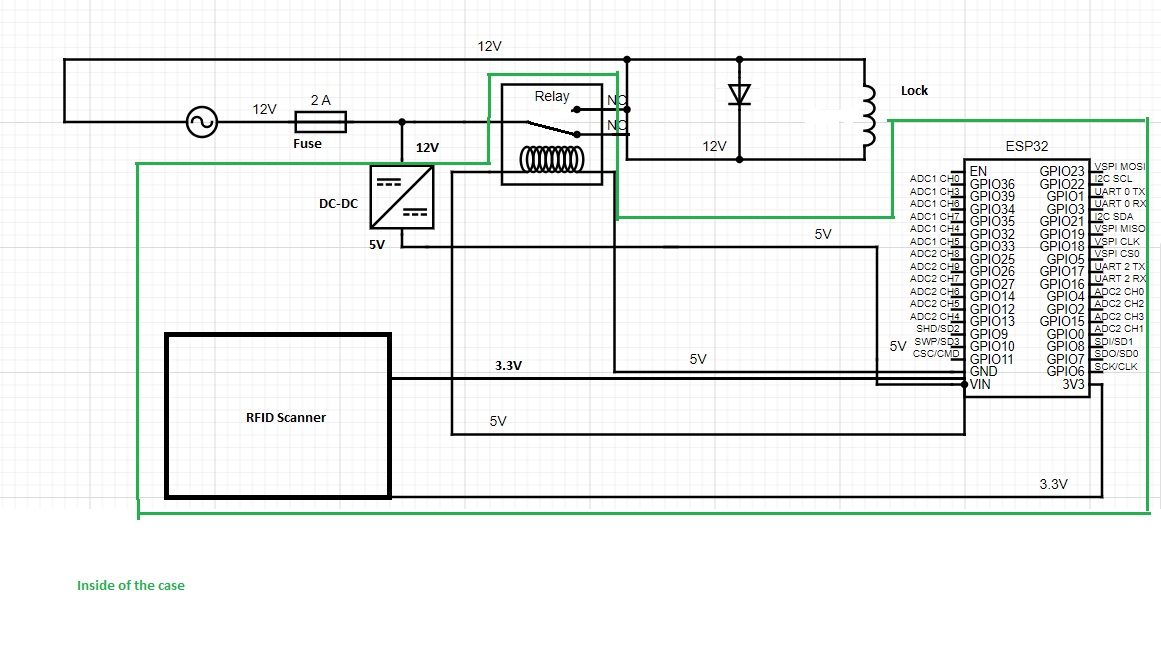
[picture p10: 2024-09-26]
schematic.jpg

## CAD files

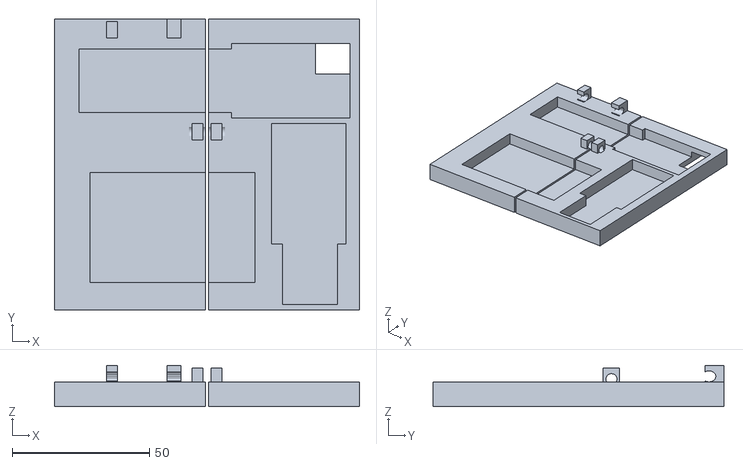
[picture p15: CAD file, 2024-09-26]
Case/WiFi frame.stl
111.0 x 106.0 x 15.0

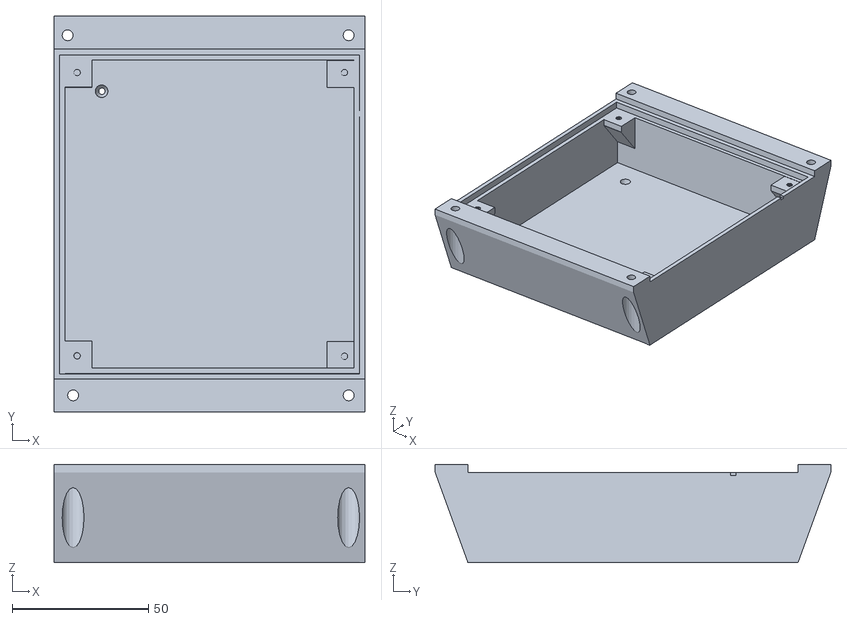
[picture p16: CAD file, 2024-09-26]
Case/Wifi Box.stl
114.0 x 145.0 x 36.0

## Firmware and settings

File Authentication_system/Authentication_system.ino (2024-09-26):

// Basic library

// WI-fI CONNECTION
#include <ESP8266WiFi.h>
#include <ESP8266HTTPClient.h>
#include <WiFiClient.h>

// RFID

#include <SPI.h>
#include <MFRC522.h>
#include <string>

// Encryption
#include "Base64A.h"

uint8_t cipher_key[16] = {0, 2, 4, 3, 4, 5, 6, 7, 8, 9, 10, 11, 12, 13, 14, 15};
uint8_t cipher_iv[16] = {0, 6, 6, 3, 4, 5, 6, 7, 8, 9, 10, 11, 12, 13, 14, 15};

// PIN SETTINGS
#define RST_PIN         D1          // Configurable, see typical pin layout above
#define SS_PIN          D2         // Configurable, see typical pin layout above
#define LIGHT_PIN       D4         // Configurable, see typical pin layout above
#define RELAY_PIN       0         // Configurable, see typical pin layout above

// Comman c++ utility
using std::vector;
using std::string;


// Wi-Fi Settings

char* ssid = "TP-LINK_6926";
char* password = "29328123";

//Your Domain name with URL path or IP address with path
String serverName = "http://192.168.0.101:8080/validateAccess";

unsigned long lastTime = 0;
unsigned long timerDelay = 5000;
vector<string> arrayString = {};
char splitCharacter = ',';


MFRC522 mfrc522(SS_PIN, RST_PIN);  // Create MFRC522 instance
MFRC522::MIFARE_Key key; 

const int lockopeningdelay = 4000; 


void setup() {
  Serial.begin(9600);
  while (!Serial);
  SPI.begin();

  mfrc522.PCD_Init();
  pinMode(RELAY_PIN, OUTPUT);
  digitalWrite(RELAY_PIN, HIGH); 
  pinMode(LIGHT_PIN, OUTPUT);
  delay(4);
// Setting Key for AES
  
  netowekCnnectWifi(ssid, password);
}

void loop() {

  if (WiFi.status() != WL_CONNECTED) {
    lightBlink(2, 500);
  }
  //Check if new tag is read by the reader 
  if ( ! mfrc522.PICC_IsNewCardPresent()) {
    return;
  }
  // Check if it is able read Serial of the tag
  if ( ! mfrc522.PICC_ReadCardSerial()) {
    Serial.print("Can t read card serial");
    return;
  }

  String ID = "";

  // Read UID of the tag
  for (byte i = 0; i < mfrc522.uid.size; i++) {
    ID.concat(String(mfrc522.uid.uidByte[i] < 0x10 ? " 0" : " ")); // copy UID
    ID.concat(String(mfrc522.uid.uidByte[i], HEX));
    delay(50);
  } 
  ID.toUpperCase();

  // if lock is open - card will close it, if lock os closed - card will open it

  if (validateUID(ID.substring(1))) {
    Serial.print("Door is open ");

    digitalWrite(RELAY_PIN, LOW);
    digitalWrite(LIGHT_PIN, HIGH);

    delay(lockopeningdelay);
    Serial.clearWriteError();

    digitalWrite(LIGHT_PIN, LOW); 
    digitalWrite(RELAY_PIN, HIGH); 
    Serial.print("Door is closed");
  } else {
    lightBlink(2,200);
    Serial.print("Wrong Card");
    Serial.clearWriteError();
  }

  digitalWrite(RELAY_PIN, HIGH); 

  Serial.println("");
  mfrc522.PICC_HaltA();
}

  // Compare UID with database

 bool validateUID(String input) {
    if ((millis() - lastTime) > timerDelay) {
    //Check WiFi connection status
      if (WiFi.status() == WL_CONNECTED) {
        WiFiClient client;
        HTTPClient http;


        String serverPath = serverName;

        // Your Domain name with URL path or IP address with path
        http.begin(client, serverPath.c_str());

        // If you need Node-RED/server authentication, insert user and password below
        //http.setAuthorization("REPLACE_WITH_SERVER_USERNAME", "REPLACE_WITH_SERVER_PASSWORD");

        // Send HTTP GET request
        http.addHeader("Content-Type", "application/x-www-form-urlencoded");
        
        //Data to send with HTTP POST
        // Serial.println("Before Encryption text main function");
        // Serial.println(input);

        // Serial.println("Encrypted text main function");
        String encdata = encrypt(input);
        Serial.println(encdata);

        // Serial.println("Decrypted text main function");
        // String decdata = decrypt(encdata);
        // Serial.println(decdata);

        String httpRequestData = "uid=" + encdata;

        // Send HTTP POST request
        int httpResponseCode = http.POST(httpRequestData);

        std::vector<String> serverData = {};

        if (httpResponseCode == -1) {
          lightBlink(6,500);
          Serial.print("Can't connect to server. Server potentially id down ");
          return false;
        }

        if (httpResponseCode > 0) {
          Serial.print("HTTP Response code: ");
          Serial.println(httpResponseCode);
          // get data
          String payload = http.getString();
          String decdata = decrypt(payload);

          // transform data to char array       
          if(decdata == "Valid" ) {
            return true;
          } else {
            return false;            
          }


        } else {
          Serial.print("Error code: ");
          Serial.println(httpResponseCode);
          return false;
        }
        // Free resources
        http.end();
      } else {
        Serial.println("WiFi Disconnected");
        return false;
      }
      
      lastTime = millis();
    }

  return false;
 }

 // AES CBC Encryption
String encrypt(String plain_data){
  int i;
  // PKCS#7 Padding (Encryption), Block Size : 16
  int len = plain_data.length();
  int n_blocks = len / 16 + 1;
  uint8_t n_padding = n_blocks * 16 - len;
  uint8_t data[n_blocks*16];
  memcpy(data, plain_data.c_str(), len);
  for(i = len; i < n_blocks * 16; i++){
    data[i] = n_padding;
  }
  
  uint8_t key[16], iv[16];
  memcpy(key, cipher_key, 16);
  memcpy(iv, cipher_iv, 16);

  // encryption context
  br_aes_big_cbcenc_keys encCtx;

  // reset the encryption context and encrypt the data
  br_aes_big_cbcenc_init(&encCtx, key, 16);
  br_aes_big_cbcenc_run( &encCtx, iv, data, n_blocks*16 );

  // Base64 encode
  len = n_blocks*16;
  char encoded_data[ base64_enc_len(len) ];
  base64_encode(encoded_data, (char *)data, len);
  
  return String(encoded_data);
}

// AES CBC Decryption
String decrypt(String encoded_data_str){  
  int input_len = encoded_data_str.length();
  char *encoded_data = const_cast<char*>(encoded_data_str.c_str());
  int len = base64_dec_len(encoded_data, input_len);
  uint8_t data[ len ];
  base64_decode((char *)data, encoded_data, input_len);
  
  uint8_t key[16], iv[16];
  memcpy(key, cipher_key, 16);
  memcpy(iv, cipher_iv, 16);

  int n_blocks = len / 16;

  br_aes_big_cbcdec_keys decCtx;

  br_aes_big_cbcdec_init(&decCtx, key, 16);
  br_aes_big_cbcdec_run( &decCtx, iv, data, n_blocks*16 );

  // PKCS#7 Padding (Decryption)
  uint8_t n_padding = data[n_blocks*16-1];
  len = n_blocks*16 - n_padding;
  char plain_data[len + 1];
  memcpy(plain_data, data, len);
  plain_data[len] = '\0';

  return String(plain_data);
}

 void netowekCnnectWifi(char* ssid, char* password) {
   
  WiFi.begin(ssid, password);
  Serial.println("Connecting");
  while (WiFi.status() != WL_CONNECTED) {
    lightBlink(2, 500);
    Serial.print(".");
  }
  Serial.println("");
  Serial.print("Connected to WiFi network with IP Address: ");
  Serial.println(WiFi.localIP());
 }

 void lightBlink(int times, int delayTime){
   for (int i=0; i <= times; i++){
    digitalWrite(LIGHT_PIN, HIGH);
    delay(delayTime);
    digitalWrite(LIGHT_PIN, LOW);
    delay(delayTime);
   }
 }

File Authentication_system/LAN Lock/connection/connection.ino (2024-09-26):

#include <SPI.h>
#include <Ethernet.h>

// replace the MAC address below by the MAC address printed on a sticker on the Arduino Shield 2
byte mac[] = { 0xDE, 0xAD, 0xBE, 0xEF, 0xFE, 0xED };

EthernetClient client;

int    HTTP_PORT   = 8080;
String HTTP_METHOD = "GET";
char   HOST_NAME[] = "192.168.0.102";
String PATH_NAME   = "";
String queryString = "";;

void setup() {
  Serial.begin(9600);

  // initialize the Ethernet shield using DHCP:
  if (Ethernet.begin(mac) == 0) {
    Serial.println("Failed to obtaining an IP address using DHCP");
    while(true);
  }

  // connect to web server on port 80:
  if(client.connect(HOST_NAME, HTTP_PORT)) {
    // if connected:
    Serial.println("Connected to server");
    // make a HTTP request:
    // send HTTP header
    client.println(HTTP_METHOD + " " + " HTTP/1.1");
    client.println("Host: " + String(HOST_NAME));
    client.println("Connection: close");
    client.println(); // end HTTP header

    while(client.connected()) {
      if(client.available()){
        // read an incoming byte from the server and print it to serial monitor:
        char c = client.read();
        Serial.print(c);
      }
    }

    // the server's disconnected, stop the client:
    client.stop();
    Serial.println();
    Serial.println("disconnected");
  } else {// if not connected:
    Serial.println("connection failed");
  }
}

void loop() {

}
